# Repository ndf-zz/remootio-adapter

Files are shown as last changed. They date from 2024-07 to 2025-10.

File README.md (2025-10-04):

# Remootio Adapter "PLC" - Hay Hoist

Adapt a Remootio door opener remote to
a golf buggy motor controller using an
AVR m328pb for remote control of a hay hoist.

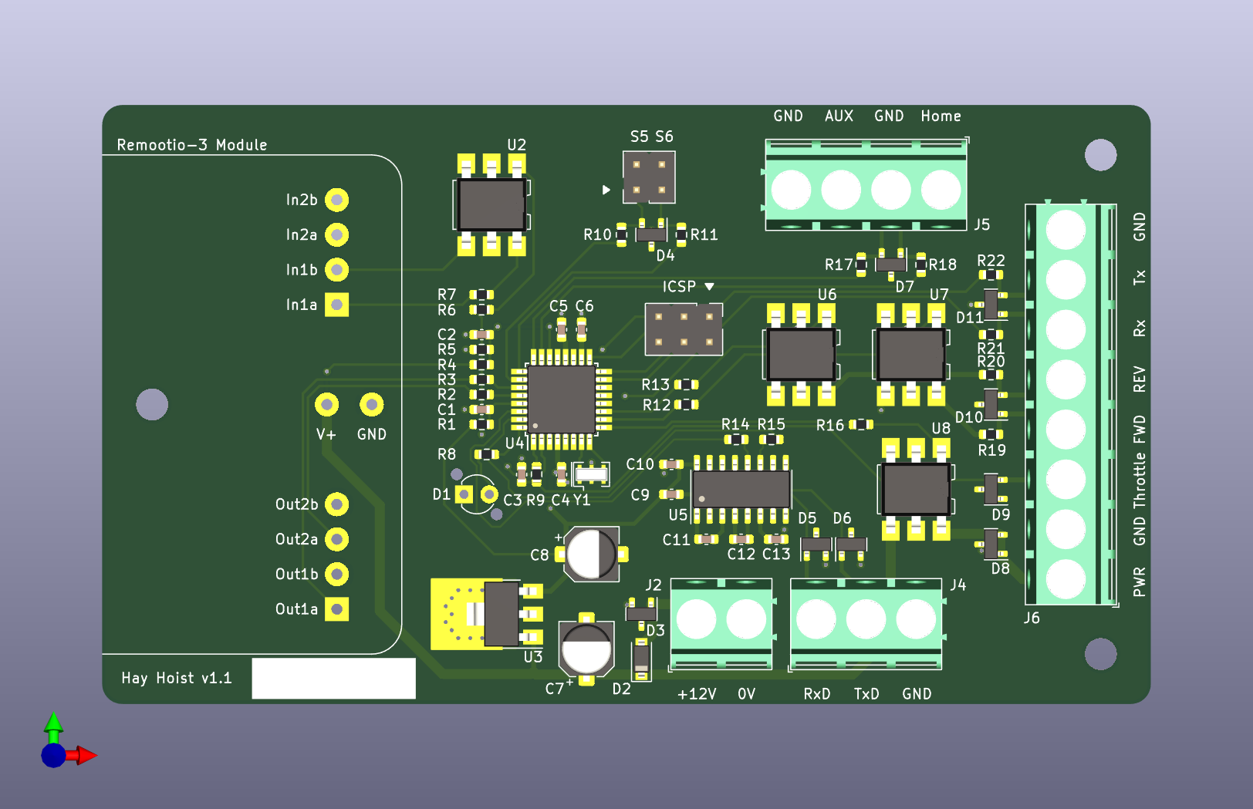
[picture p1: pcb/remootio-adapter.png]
PCB


## Operation

### Manual Operation

On reception of "down" command, hoist is lowered to P1 height.
If no further commands are received, it will retract to the home
position after the configured feed time minutes have elapsed.

A further "down" command will lower the hoist to the P2 height.

Return to home position on reception of an "up" signal, or
after a programmable duration without input.

State Machine State Diagram

### Automated Feeding

If a number of feeds per week is specified, the hoist will lower
from the home position to P1 after a randomly chosen interval,
roughly "feeds/week" times a week and provided there is enough
charge in the battery to retract.

The hoist will remain at P1 until feed time minutes have elapsed, 
then retract to the home position. Manual operation "down" or
"up" will cancel a pending automatic operation.

To disable automated feeding, manually lower the hoist slightly
from the home position. To re-enable, return hoist to home
("open") position.

### Special Cases

If an error condition is flagged, the hoist will only allow
movement up and down small amounts determined by the "Man time"
setting. To correct an error state, clear the sensor
switch and then manually operate the hoist down slightly and
then up to the home position.

Errors and exceptions may be triggered by the following conditions:

   - Low Battery: Automated feeding is suppressed when battery
     voltage falls below 13V. In this state, manual operation
     is still enabled. If the battery falls below 11.8V,
     a warning LED is illuminated and remootio operation is disabled.
   - Spurious Sensor: In the case of a spurious triggering of
     the home sensor, an error condition is flagged and the
     motor is stopped.
   - Not at Home: If the home sensor is prematurely
     triggered, the hoist will attempt to continue retraction
     after Home-Retry seconds.
   - Sensor Failure: If the home sensor fails "open", or if the
     state logic is out of sync, the hoist will not react to
     up (raise) commands. If the sensor fails "closed", and max
     H time has elapsed, the hoist will flag an error condition.
   - Safetime: If the hoist is left at position P2, between P1 and P2,
     or in the STOP state, it will attempt to retract automatically
     to the home position after about 60 minutes.
   - Disable Automation: Automated random feeding may be temporarily
     disabled by manually lowering the hoist slightly from the home
     position to state "STOP H-P1". To re-enable random feeding, return
     hoist to home position.

### Serial Console

**Note**: Serial console is not available on units supplied with
BLE adapter.

Connect RS-232 serial adapter to J4 (console)
and open a terminal at 19200 baud, 8n1.

Enter 'p' followed by pin number and enter to enable
console.

Triggers, state changes and errors will
be displayed.

Enter '?' to display available commands:

	Commands:
	        1       H-P1 (0.01s)
	        2       P1-P2 (0.01s)
	        m       Man (0.01s)
	        h       H (0.01s)
	        r       H-Retry (0.01s)
	        f       Feed (minutes)
	        n       Feeds/week (0=off)
	        v       Show values
	        s       Status
	        d       Lower
	        u       Raise

Configuration parameters are adjusted
by entering the command key followed by
an updated value and then enter.
Time values 1,2,m,h and r are set in units of 0.01s.
Feeding time f is in minutes.

## Connectors

Adapter | Connector | Description
--- | --- | ---
J1:1 |  | "S5" Auxiliary I/O (unused)
J1:2 |  | "GND"
J1:3 |  | "S6" Auxiliary I/O (unused)
J1:4 |  | "GND"
N/C | C3:B | Motor + (blue/black)
N/C | C3:C | Motor - (yellow/red)
J2:1 | C4:D | "+12V" Battery + (red)
J2:2 | C4:A | "0V" Battery - (black)
J3:1 |  | ICSP MISO
J3:2 |  | ICSP VCC
J3:3 |  | ICSP SCK
J3:4 |  | ICSP MOSI
J3:5 |  | ICSP RST
J3:6 |  | ICSP GND
J4:1 | C1:2 | "RxD" Console DCE Received Data (brown)
J4:2 | C1:3 | "TxD" Console DCE Transmitted Data (yellow)
J4:3 | C1:5 | "GND" Console DCE Common Ground (white)
J5:1 | C2:C | "Home" Home Limit Input (NC output green)
N/C | C2:B | Short to C2:D (green)
J5:2 | C2:A | "GND" Home Limit Ground (blue)
N/C | C2:D | Short to C2:B
J5:3 |  | "AUX" Encoder/Counter Input (unused)
J5:4 |  | "GND" Encoder/Counter Ground
J6:1 | M1:7 | "PWR" Controller power (pink)
J6:2 | M:6,20 | "GND" Controller ground (black)
J6:3 | M:3 | "Throttle" Controller speed (green)
J6:4 | M:12 | "FWD" Controller forward (white)
J6:5 | M:14 | "REV" Controller reverse (orange)
J6:6 | M:Rx | "Rx" Controller serial receive (blue)
J6:7 | M:Tx | "Tx" Controller serial transmit (green)
J6:8 | M:Gnd | "GND" Controller ground (black)

## Firmware

### Source Layout

	Main event loop:		src/main.c: 	main()
	State machine logic:	src/main.c:		update_state()
	Reset/initialisation:	src/system.c:	system_init()
	Serial console logic:	src/console.c:	read_input()
	SPM controller setting:	src/spmcheck.c	spm_check()

### Version Summaries

   - 25003: BLE adapter updates, October 2025
      - include system clock with state summary
      - adjust low battery override states
      - extend console idle timeout to 5 minutes
      - extend safe time to 60 minutes
   - 25002: Version 2.1, ignore home trigger when at P1
   - 25001: Version 2
      - include Home Retry option & logic
      - add trivial plaintext 'passkey' to protect serial console
   - 24012: Version 1, cosmetic updates for GUI tool, October 2024
   - 24011: Version 0, initial release September 2024

## Build

Connect AVR ISP to programming header, program fuses, initialise
the random seed book, then build and upload firmware to MCU:

	$ make fuse
	$ make randbook
	$ make upload

Note: randbook will overwrite any stored configuration, so it should
only be run once when initialising a new unit. Uploading a new
firmware will not overwrite stored configuration.

On boot, the SPM controller will be updated if required. Updates are
reported to the console output:

	Info: Boot v24011
	SPM: Config updated
	Info: Boot v24011
	SPM: 23014810
	Trigger: reset
	State: [STOP] Batt: 0.0V
	Trigger: home
	[...]

## Build Requirements

   - GNU Make
   - gcc-avr
   - binutils-avr
   - avr-libc
   - avrdude
   - python3 (if controller config is edited)

On a Debian system, use make to install required packages:

	$ make requires

## Production Unit Info

   - [assembly/](assembly/ "Assembly instruction")
   - [assembly/burn-in.sh](assembly/burn-in.sh "Burn-in"):
     Prepare unit for first-time use.
   - [assembly/update25001.sh](assembly/update25001.sh "Update to v25001+"):
     Update unit with firmware < v25001, retaining configuration.

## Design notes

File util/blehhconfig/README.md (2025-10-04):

# Hay Hoist Bluetooth Configuration Tool

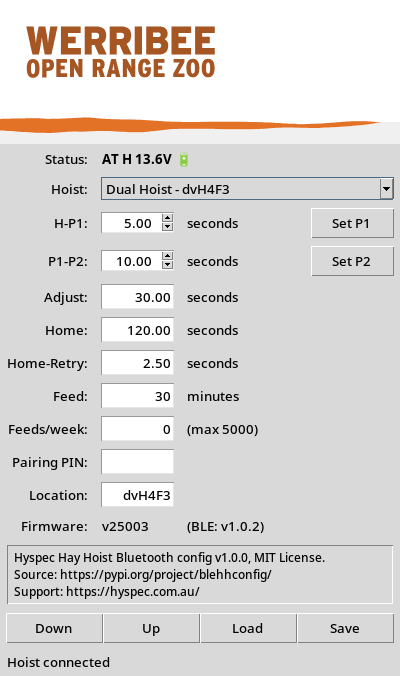
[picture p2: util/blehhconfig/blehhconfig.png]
blehhconfig screenshot


Configure Hay Hoist connected via a
[bleuart](https://github.com/ndf-zz/bleuart/)
Bluetooth to RS232 adapter.

## Usage

	blehhconfig [-v]

Launch blehhconfig utility, then select hoist from
devices list.

Current status is displayed on the top line. Use
"Down" and "Up" buttons to trigger the hoist. "Load"
and "Save" buttons read or write configuration
from/to a JSON text file.

Set P1 and Set P2 buttons measure time and update
a connected hoist accordingly.

## Installation

Install into a venv with pip:

	$ python -m venv hh
	$ ./hh/bin/pip install blehhconfig
	$ ./hh/bin/blehhconfig

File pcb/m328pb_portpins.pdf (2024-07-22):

Hay Hoist - ATmega328PB Port/Pin Allocation

Date: 2024-07-22

# Channel

Port | 0 | 1 | 2 | 3 | 4 | 5 | 6 | 7
B | | | | X | X | S | S | S | Unused/Not available
| | | | MTX | MRX | SCK | XTAL1 | XTAL2
C | I | I | I | I | I | I | S | | USART
| S1 | S2 | S6 | S5 | S3 | S4 | RESET
D | X | X | O | X | O | O | O | O | Out
| CRX | CTX | LED | V1(PWM) | R4 | R3 | R1 | R2
E | | | | A | | | | | In
| | | | A1
| Pin Modes | | Signals
I: Digital Input | V1 | Throttle (0-5V) | S1 - S6 | Switch Inputs 1-6
O: Digital Output | A1 | Battery Sense | R1 - R4 | Relay Outputs 1-4
A: Analog | MTX/RX | Motor Serial Port | LED | Indicator LED
X: Alternate Function | CTX/CRX | Console Serial Port

S: Additional Function

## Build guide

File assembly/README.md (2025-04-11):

# Assembly Instruction

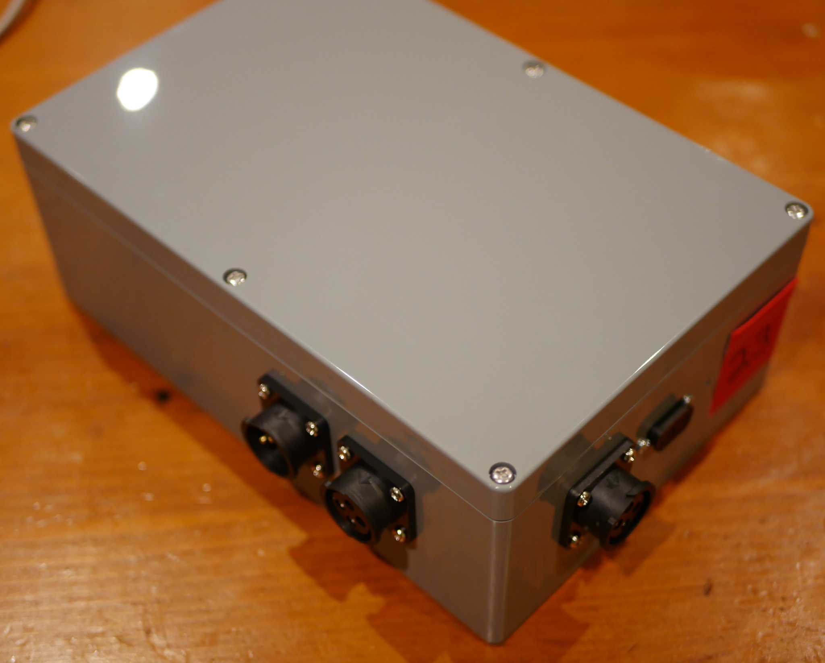
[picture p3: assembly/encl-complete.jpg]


## Components

   - Remootio Module
   - Main PCB
   - Motor Controller
   - Connectors
   - Mounting Plate
   - Enclosure
   - AC Power Supply

## Remootio Module

Power on Remootio using supplied DC adapter, pair with
application and then setup as follows:

   - Select output configuration 4: "Output 1 to open, Output 2 to close"
   - Configure both "open" and "close" impulse length to 50ms.
   - Disable background display option
   - Under power settings enable "Low Power Mode" and "Dark Mode"
   - Enable sensor add-on: Input 1

Test operation with application, then prepare PCB for use with
adapter:

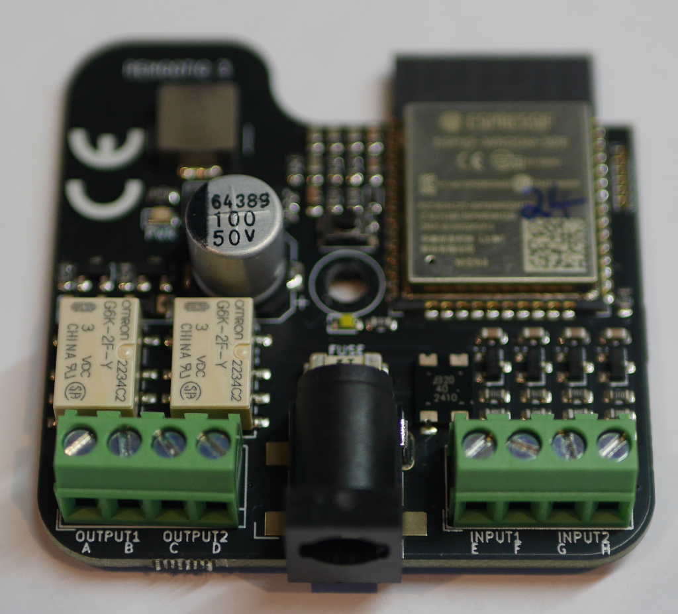
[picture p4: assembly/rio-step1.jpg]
Remove Enclosure


Remove Remootio from plastic enclosure.

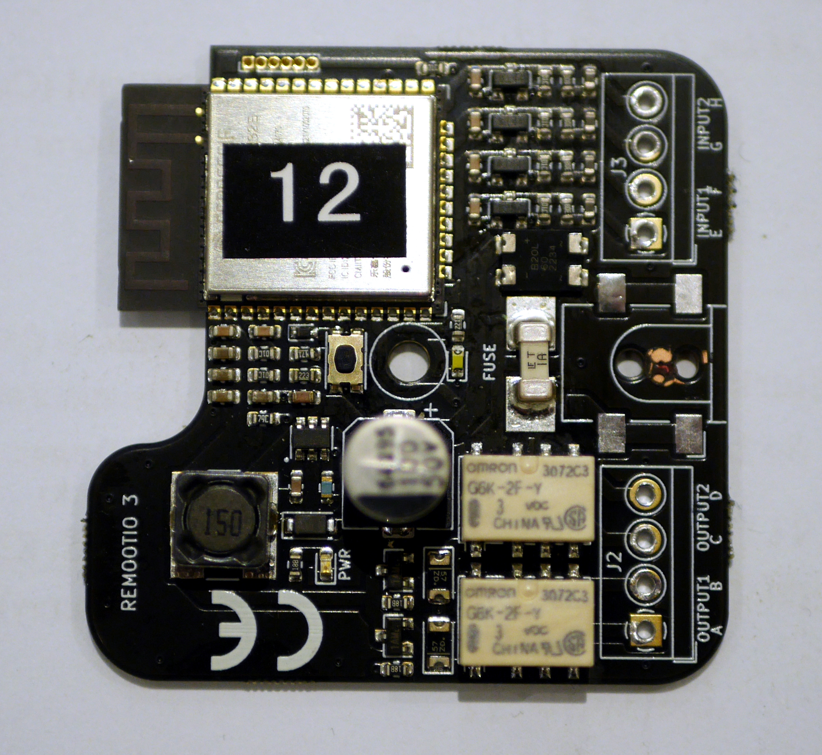
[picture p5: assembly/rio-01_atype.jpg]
SMT Variant SMT DC Variant


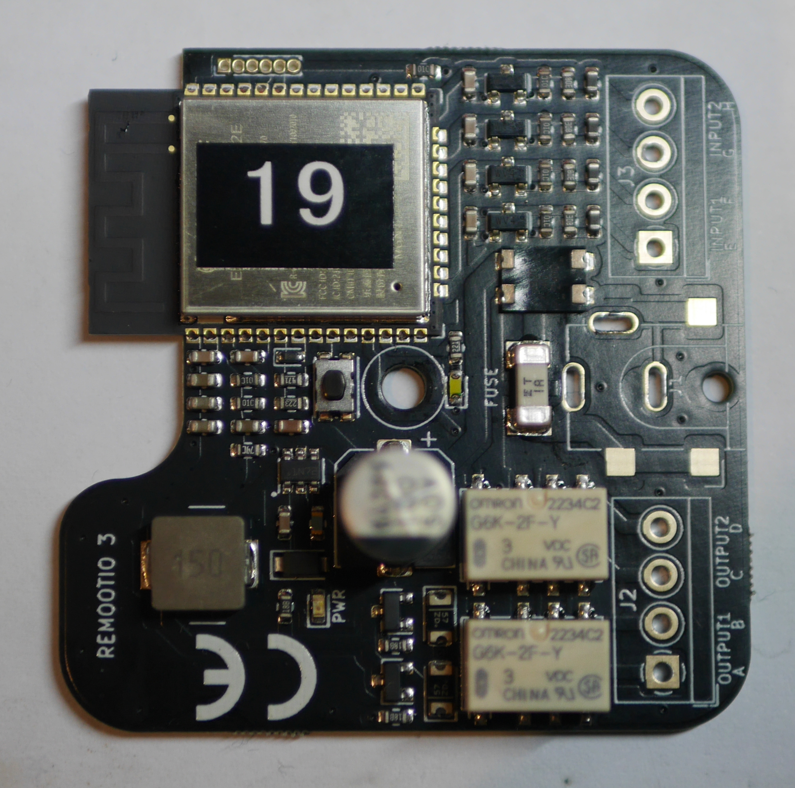
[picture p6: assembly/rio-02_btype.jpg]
THT Variant THT DC Variant


De-solder DC socket and screw terminal blocks.

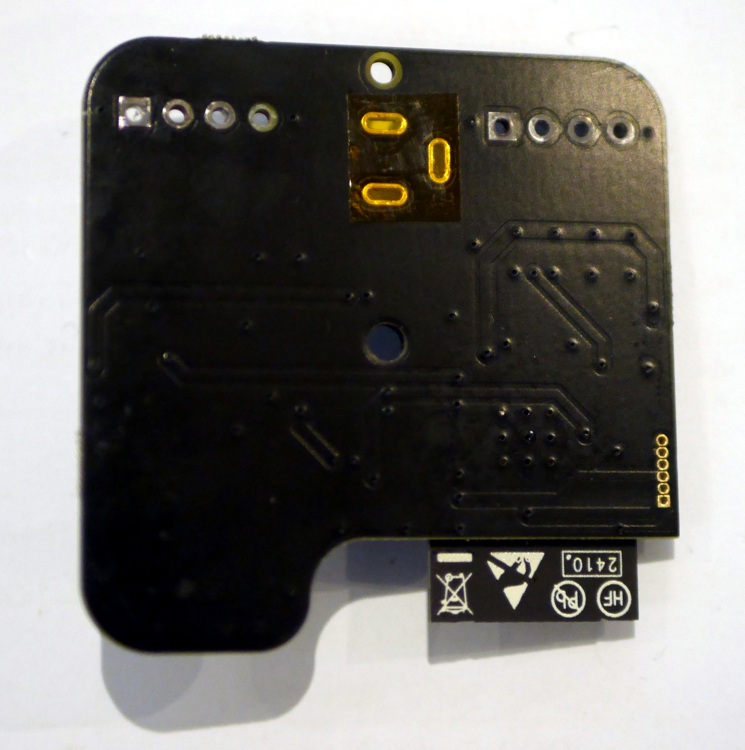
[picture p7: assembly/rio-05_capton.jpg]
Capton THT THT Capton Tape


If DC connector is through-hole type, place a strip of capton tape
over bottom-side pads.
For both variants, place small length of
capton tape over DC jack alignment hole(s) on top side.

Label module with serial number for future reference.

## Main PCB

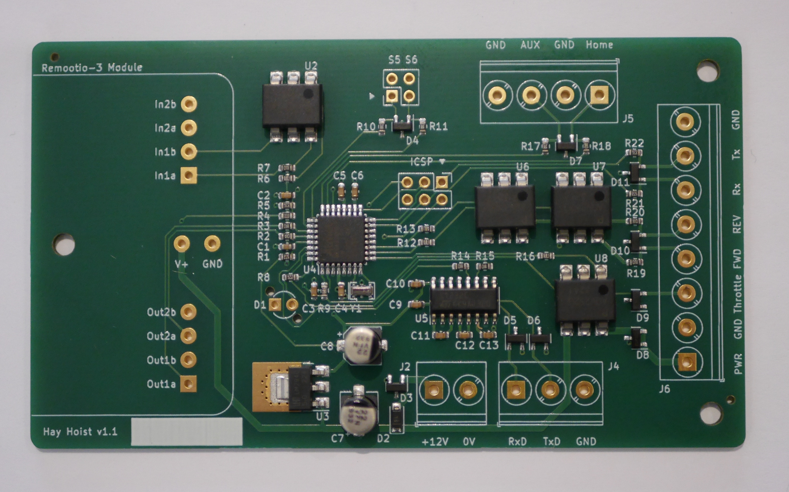
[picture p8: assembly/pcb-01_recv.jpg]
Inspect Inspect PCB


Inspect PCB for clean solder joints, parts properly located
and finish.

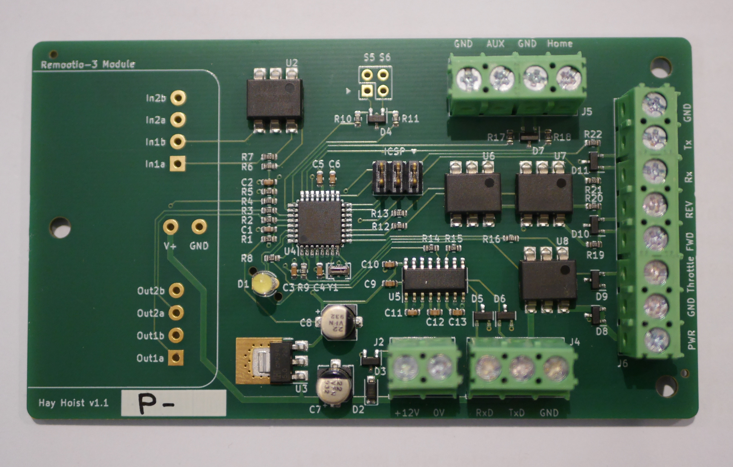
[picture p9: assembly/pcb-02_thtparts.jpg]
THT Parts Solder THT Parts


Solder THT parts to PCB:

   - ICSP header J3
   - Screw terminals J2, J4, J5, J6
   - LED D1 with ~4mm standoff from board

Perform the following tests:

   - connect console C1 and 12V
   - connect ICSP
   - power on
   - run burn-in.sh
   - observe boot sequence
   - verify home trigger
   - stimulate home trigger, observe console
   - short home trigger
   - command up, check for spurious warning
   - set meter to Volts, command down
      - check PWR at ~12V
      - check Throttle at ~5V
   - set meter to continuity
      - check In1a/b for short AT-P1
      - Check FWD & REV open to GND
      - command up/down & check FWD/REV short to GND
   - observe console
      - trigger Out1a/b and Out2a/b for up/down trigger
   - pass => write "P-" on serial no panel

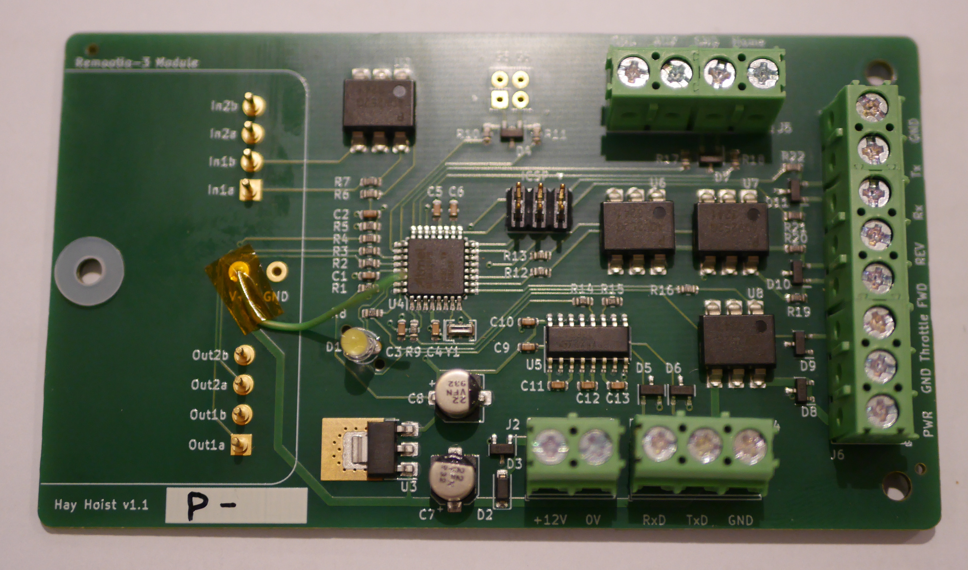
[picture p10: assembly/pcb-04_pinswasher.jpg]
RIO Mounting Remootio Pins


Insert Remootio module mounting pins (do not solder). If Remootio
is THT type, insert a short bodge wire as pictured and
cover with capton tape. Position 2x spacing washers over mounting
hole, then lower module into place and fix with screw.

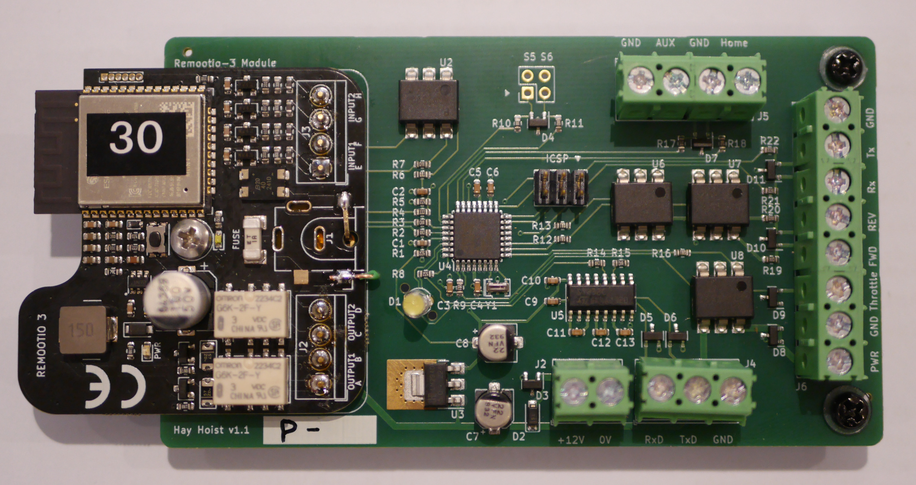
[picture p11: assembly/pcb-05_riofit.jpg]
THT RIO Solder THT Type Soldered


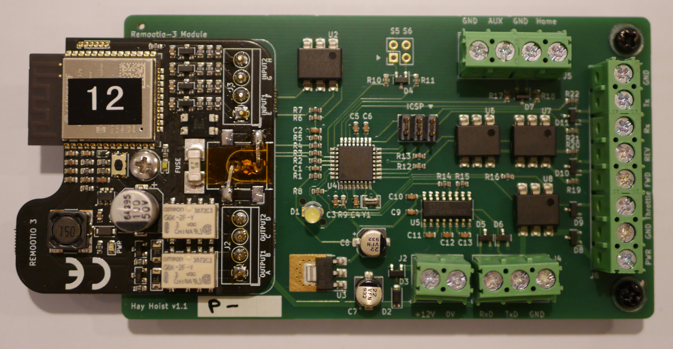
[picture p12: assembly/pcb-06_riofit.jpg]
SMT RIO Solder SMT Type Soldered


Solder mounting pins and power links from top side, then flip
board and solder bottom side.

Power on unit and check operation of Remootio on adapter.

## Motor Controller Preparation

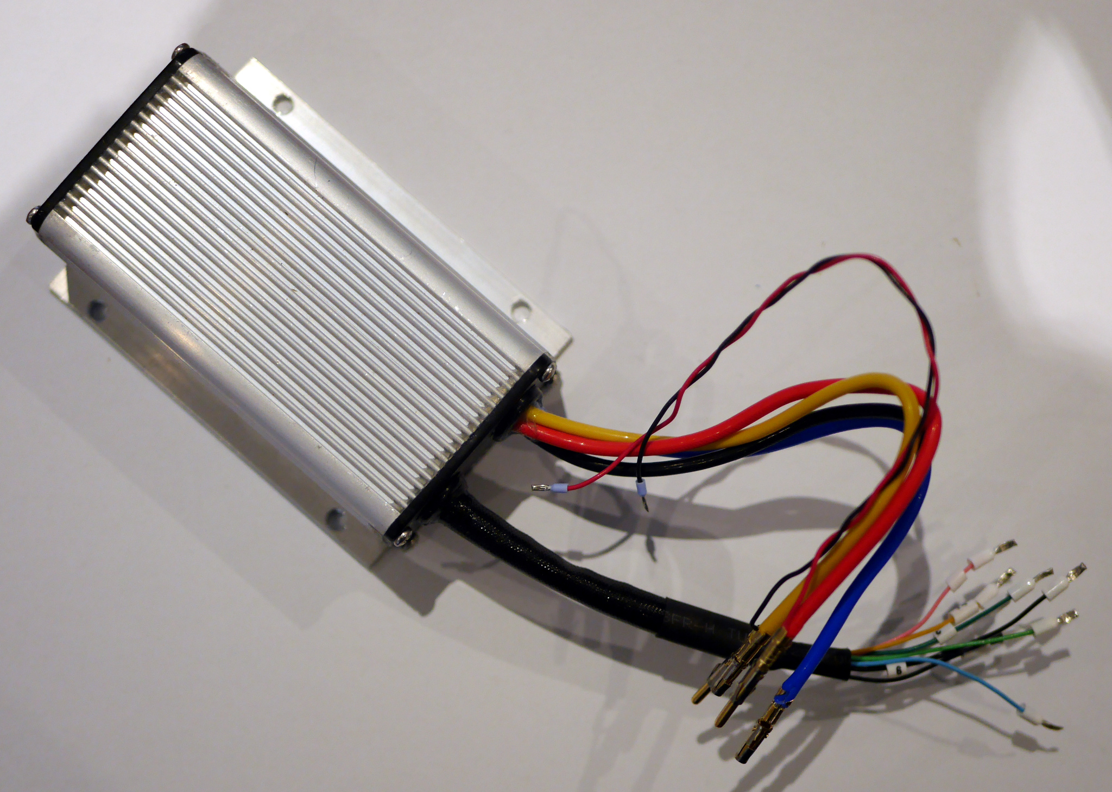
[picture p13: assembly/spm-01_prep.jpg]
Motor Controller


Shorten cable sleeve 15-20mm. At the serial connector,
cut the red (V+) wire. At the other connectors,
cut the following unused wires:

   - 1 Raddle[sic] (BRK2)
   - 2 Dark Gray (Brake AN)
   - 4 Purple (5V)
   - 8 Blue (Meter)
   - 9 Light Blue (Relay)
   - 10 Yellow (Alarm)
   - 11 Red (12V)
   - 13 Brown (BRK_SW)
   - 15 Gray (Micro SW)
   - 22 Blue/Green (undocumented)

Thread unused wires under heat-shrink, check required
wires are still attached, then cut short.
Terminate required wires with crimp ferrules:

   - 7 Pink J6:1 (PWR)
   - 6 & 20 Black J6:2 (GND, terminate together)
   - 3 Dark Green J6:3 (Throttle, may be light green)
   - 12 White J6:4 (FWD)
   - 14 Orange J6:5 (REV_SW, may be yellow)
   - Serial Blue J6:6 (Rx)
   - Serial Green J6:7 (Tx)
   - Serial Black J6:8 (GND)

Terminate blue and yellow motor leads with female
crimp terminals (SS12A1F).

Twist ~200mm length of red and black hookup wire on to
corresponding battery leads, then terminate with male
crimp terminals (SP12A1F).

Terminate loose ends of red/black hookup wires with crimp ferrule.

Motor controller is configured by firmware at boot time
as necessary according to
[spm_config.bin](../reference/spm_config.bin)
and [spm_config.txt](../reference/spm_config.txt).

Use [spmtool](https://github.com/ndf-zz/spmtool) to create
a new configuration if required. Settings match the following in
Kelly Controller software:

### Step 1: General Setting

   - Forward Switch: Enable
   - Foot Switch: Disable
   - Throttle Sensor Type: 0-5V
   - Throttle Effective Starting: 4%
   - Throttle Effective Ending: 96%
   - Max Motor Current: 85%
   - Max Battery Current: 40%

### Step 2: General Setting

   - Start-up Delay: 0 sec
   - Control Mode: Balanced
   - Under voltage: 10V
   - Over Voltage: 20V
   - Throttle Up/Down Rate: 1 (Fast)
   - Power On High Pedal Disable: Disable
   - Releasing Brake High Pedal Disable: Disable

### Step 3: General Setting

   - Motor Top Speed: 100%
   - Boost Function: Disable
   - Economy Function: Disable
   - Half Current in Reverse: Disable
   - ABS: Disable
   - 12V Output: Disable
   - Motor Top Speed in Reverse: 100%
   - Joysticker[sic] Throttle: Disable

### Step 4: Regeneration Setting

   - Regeneration: Disable
   - Brake Switch: Disable
   - Releasing Throttle Starts Regen: Disable
   - Regen Current By Brake Switch On: 5% [unused]
   - Max Regen Current: 20% [unused]
   - Brake Sensor Type: No
   - Brake Sensor Starting Point: 0% [unused]
   - Brake Sensor Ending Point: 100% [unused]

### Step 5: Sensor, CAN, Smooth Setting

   - Motor Temperature Sensor: Disable
   - Controller Stop Output Temperature: 125C
   - Controller Resume Output 90C
   - CAN [empty]
   - Smooth: Disable

## Console Port C1

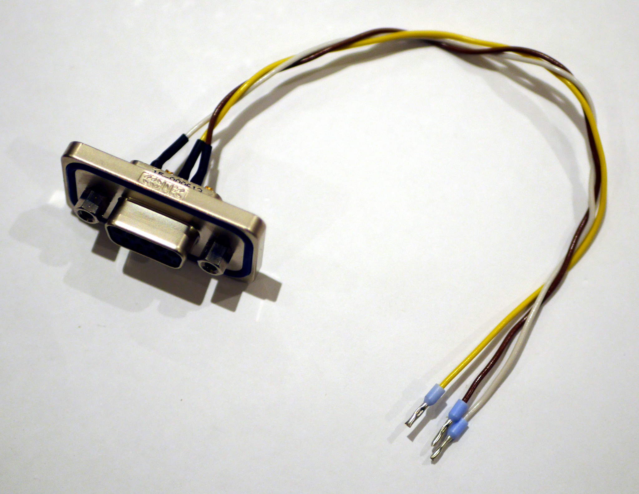
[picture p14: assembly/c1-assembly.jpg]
Console Port Console Port C1


Solder ~170mm wires to console dsub-9 (15-000613)
pins as follows:

   - Brown: C1:2 / J4:1 "RxD"
   - Yellow: C1:3 / J4:2 "TxD"
   - White: C1:5 / J4:3 "GND"

Terminate J4 ends with crimp ferrule.

## Sensor Port C2

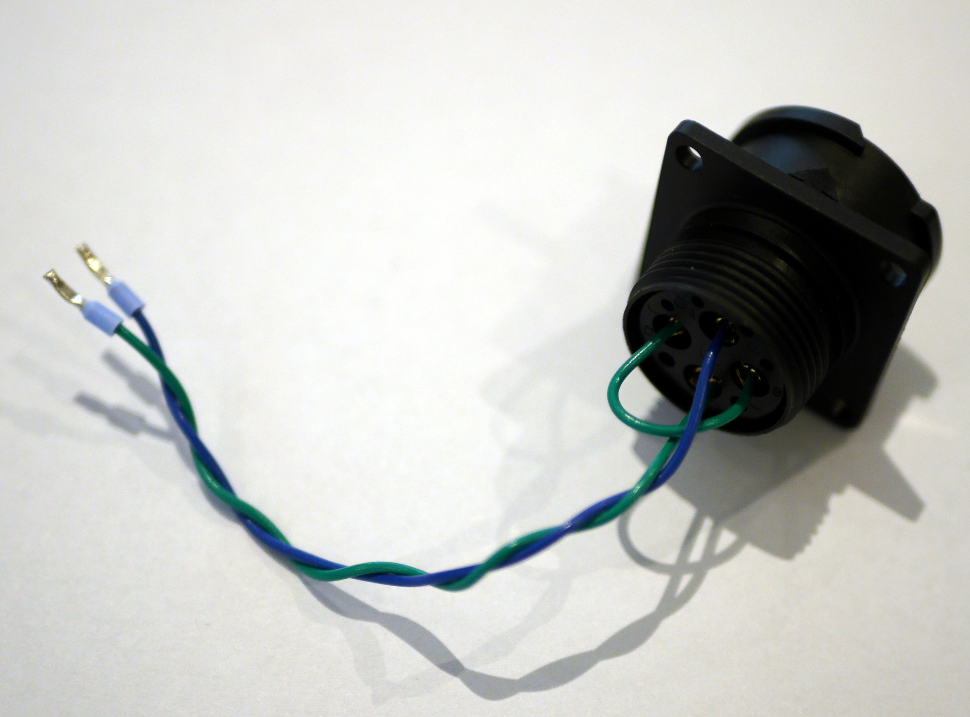
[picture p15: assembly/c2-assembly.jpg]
Sensor Port Sensor Port C2


Terminate ~90mm wires to female connector (SS12A1F):

   - Blue: C2:A / J5:2
   - Green: C2:C / J5:1

Short C2:B to C2:D with short link wire (green) and install
in female panel socket (FLS014N4S03-PM). Terminate
J5 ends with crimp ferrule.

## Enclosure

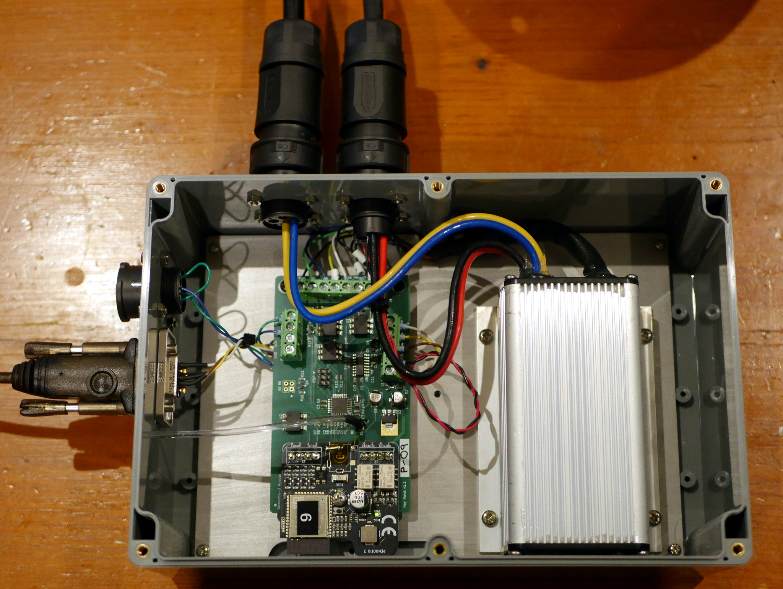
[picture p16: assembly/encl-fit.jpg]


   - Drill 2.9mm LED hole and D-SUB corners
   - Drill 3.2mm mounting holes and connector centres
   - Drill 5.5mm D-SUB corners
   - Enlarge connector holes to 21.0mm
   - Route D-SUB edges
   - Remove Burrs
   - Mount connectors to outside of case, add screws and fix
     with a small amount of thread lock on the nuts
   - Assemble PCB and motor controller on mounting plate
   - Connect wiring sub-assemblies to PCB
   - Lower complete mounting plate into box, fix with 4x M3
     screws with a small amount of thread locker
   - Insert sensor wires into connector
   - Mount D-SUB connector and tie leads to sensor wires
   - Thread LED pipe from outside box
   - Place 25mm length of heat-shrink over LED, insert LED pipe
     and shrink
   - Insert power cables and motor cables
   - Check operation in test harness
   - Fit lid and tighten

## AC Power Supply (indoor units)

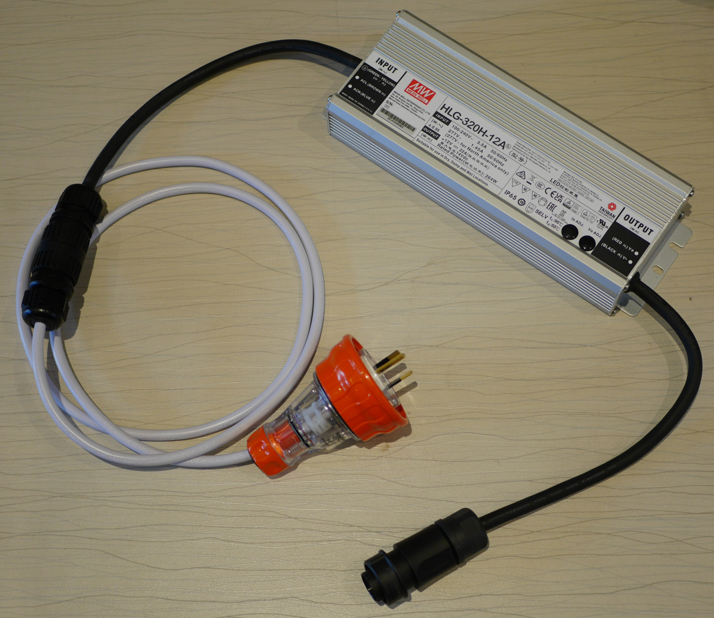
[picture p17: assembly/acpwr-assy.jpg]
AC Assembly AC Adapter Assembly


Prepare 12V connector (FLS6BS14N4S03):

   - insert rubber gland into backshell
   - slip nut and backshell over wire
   - terminate 12V lead with female terminals (SS12A1F)
   - insert 0V (black) terminal into position A
   - insert +12V (red) terminal into position D
   - tighten backshell and lock nut

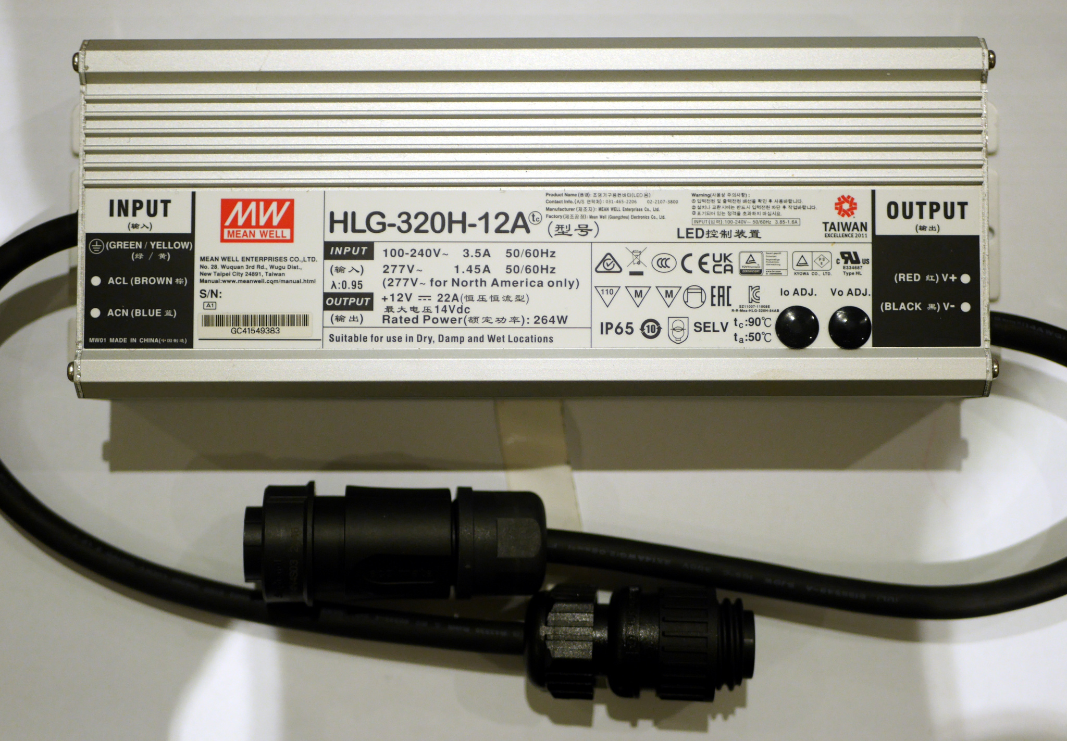
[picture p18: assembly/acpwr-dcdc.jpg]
Adapter AC Adapter


Prepare mains input plug (CA3LS):

   - crimp red ferrule on A, N and E wires
   - insert rubber gland into backshell
   - slip nut and backshell over wire
   - screw terminals into plug:
      - E position "PE"
      - A position 1
      - N position 2
   - tighten backshell and lock nut

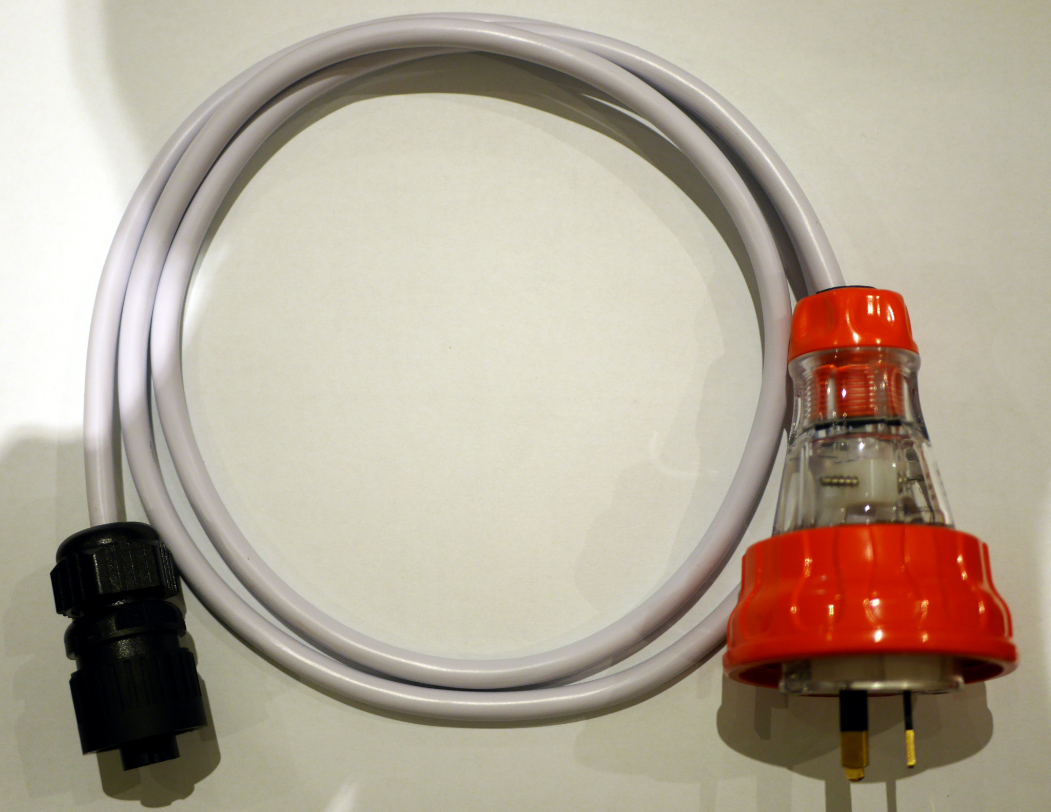
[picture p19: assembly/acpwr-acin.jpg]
AC Extension


Prepare mains extension lead:

   - cut mains lead to required length ~1500mm
   - strip ~28mm leads on both ends
   - terminate all ends with red crimp ferrules
   - mount captive IEC plug as per manufacturer instruction
   - insert rubber gland in plug backshell (CA3LD)
   - slip nut and backshell over wire
   - screw terminals into plug:
      - E position "PE"
      - A position 1
      - N position 2
   - tighten backshell and lock nut

Connect to power and box, then adjust Vo to 13.5V
Confirm Battery reading in config tool between 13.3 and 13.6V

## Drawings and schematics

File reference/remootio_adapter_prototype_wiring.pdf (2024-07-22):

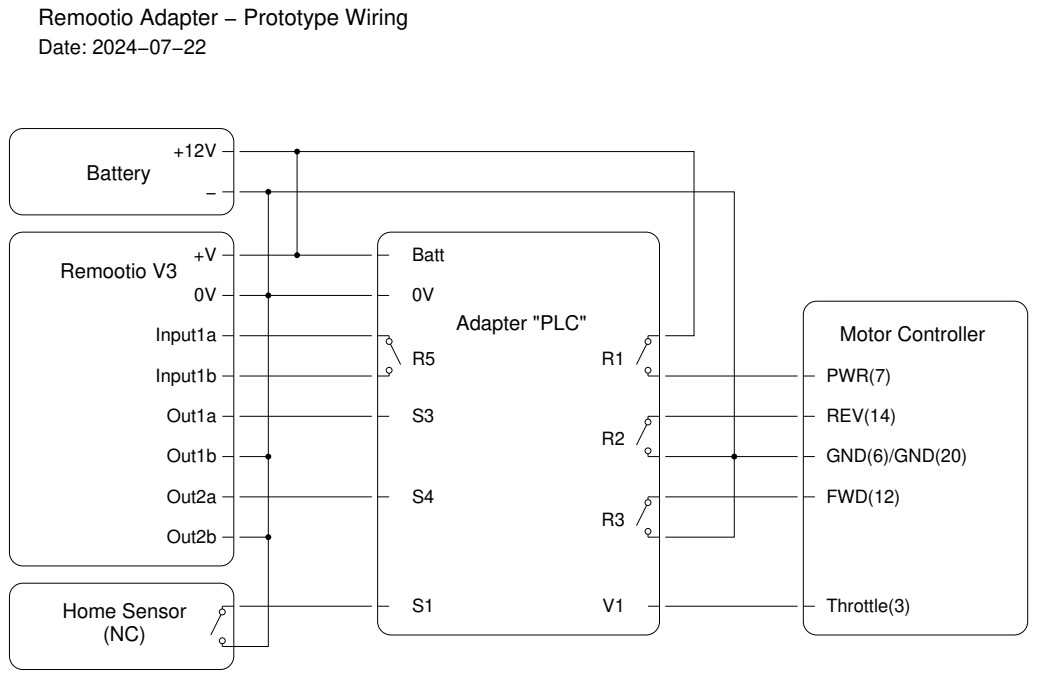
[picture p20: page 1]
Battery; Out1a; Input1a; Input1b; Out1b; Out2a; Out2b; Remootio V3; Home Sensor (NC); Adapter "PLC"; Throttle(3); REV(14); FWD(12); PWR(7); GND(6)/GND(20); Motor Controller; Batt

Remootio Adapter − Prototype Wiring
Date: 2024−07−22

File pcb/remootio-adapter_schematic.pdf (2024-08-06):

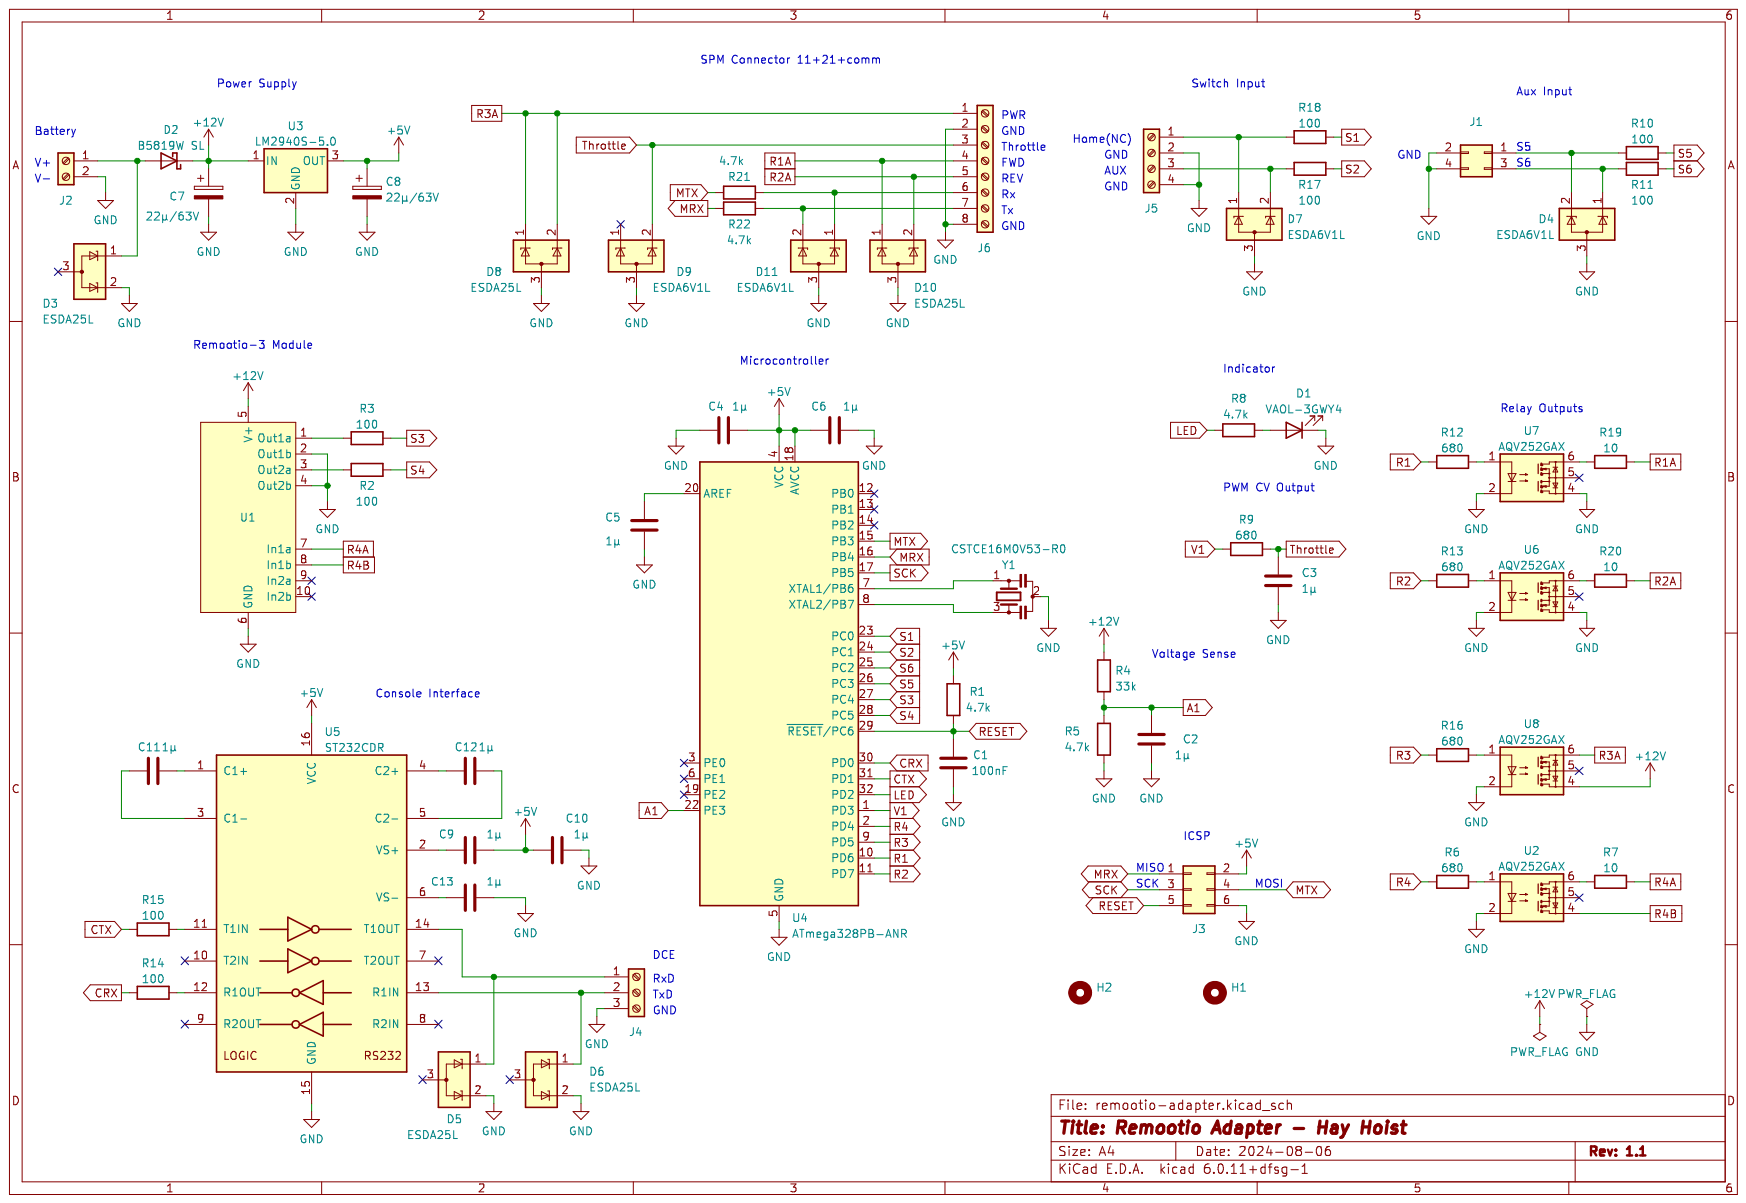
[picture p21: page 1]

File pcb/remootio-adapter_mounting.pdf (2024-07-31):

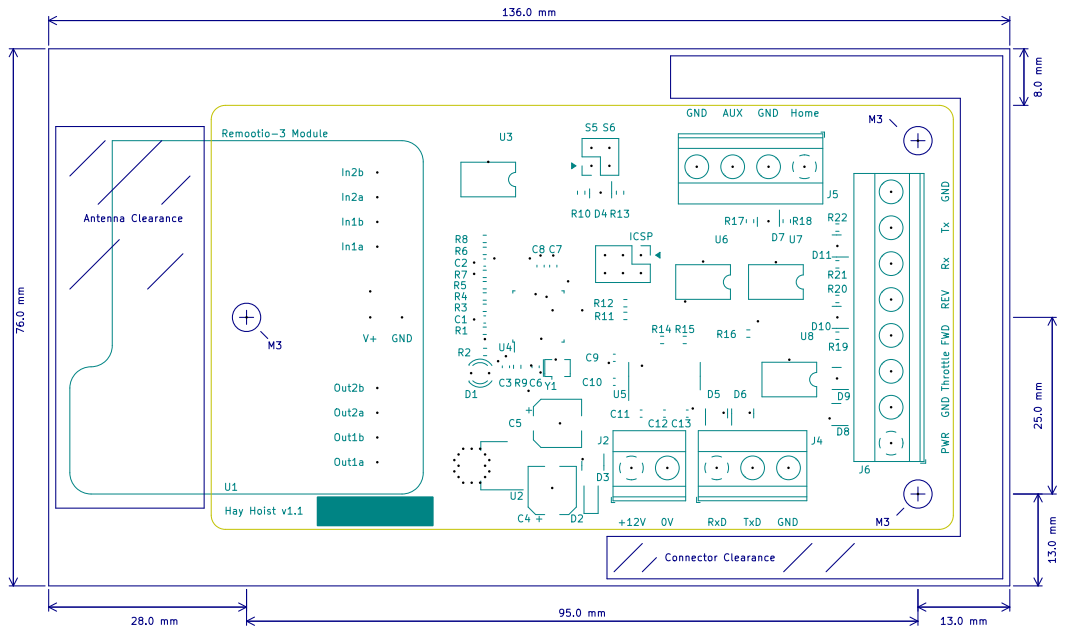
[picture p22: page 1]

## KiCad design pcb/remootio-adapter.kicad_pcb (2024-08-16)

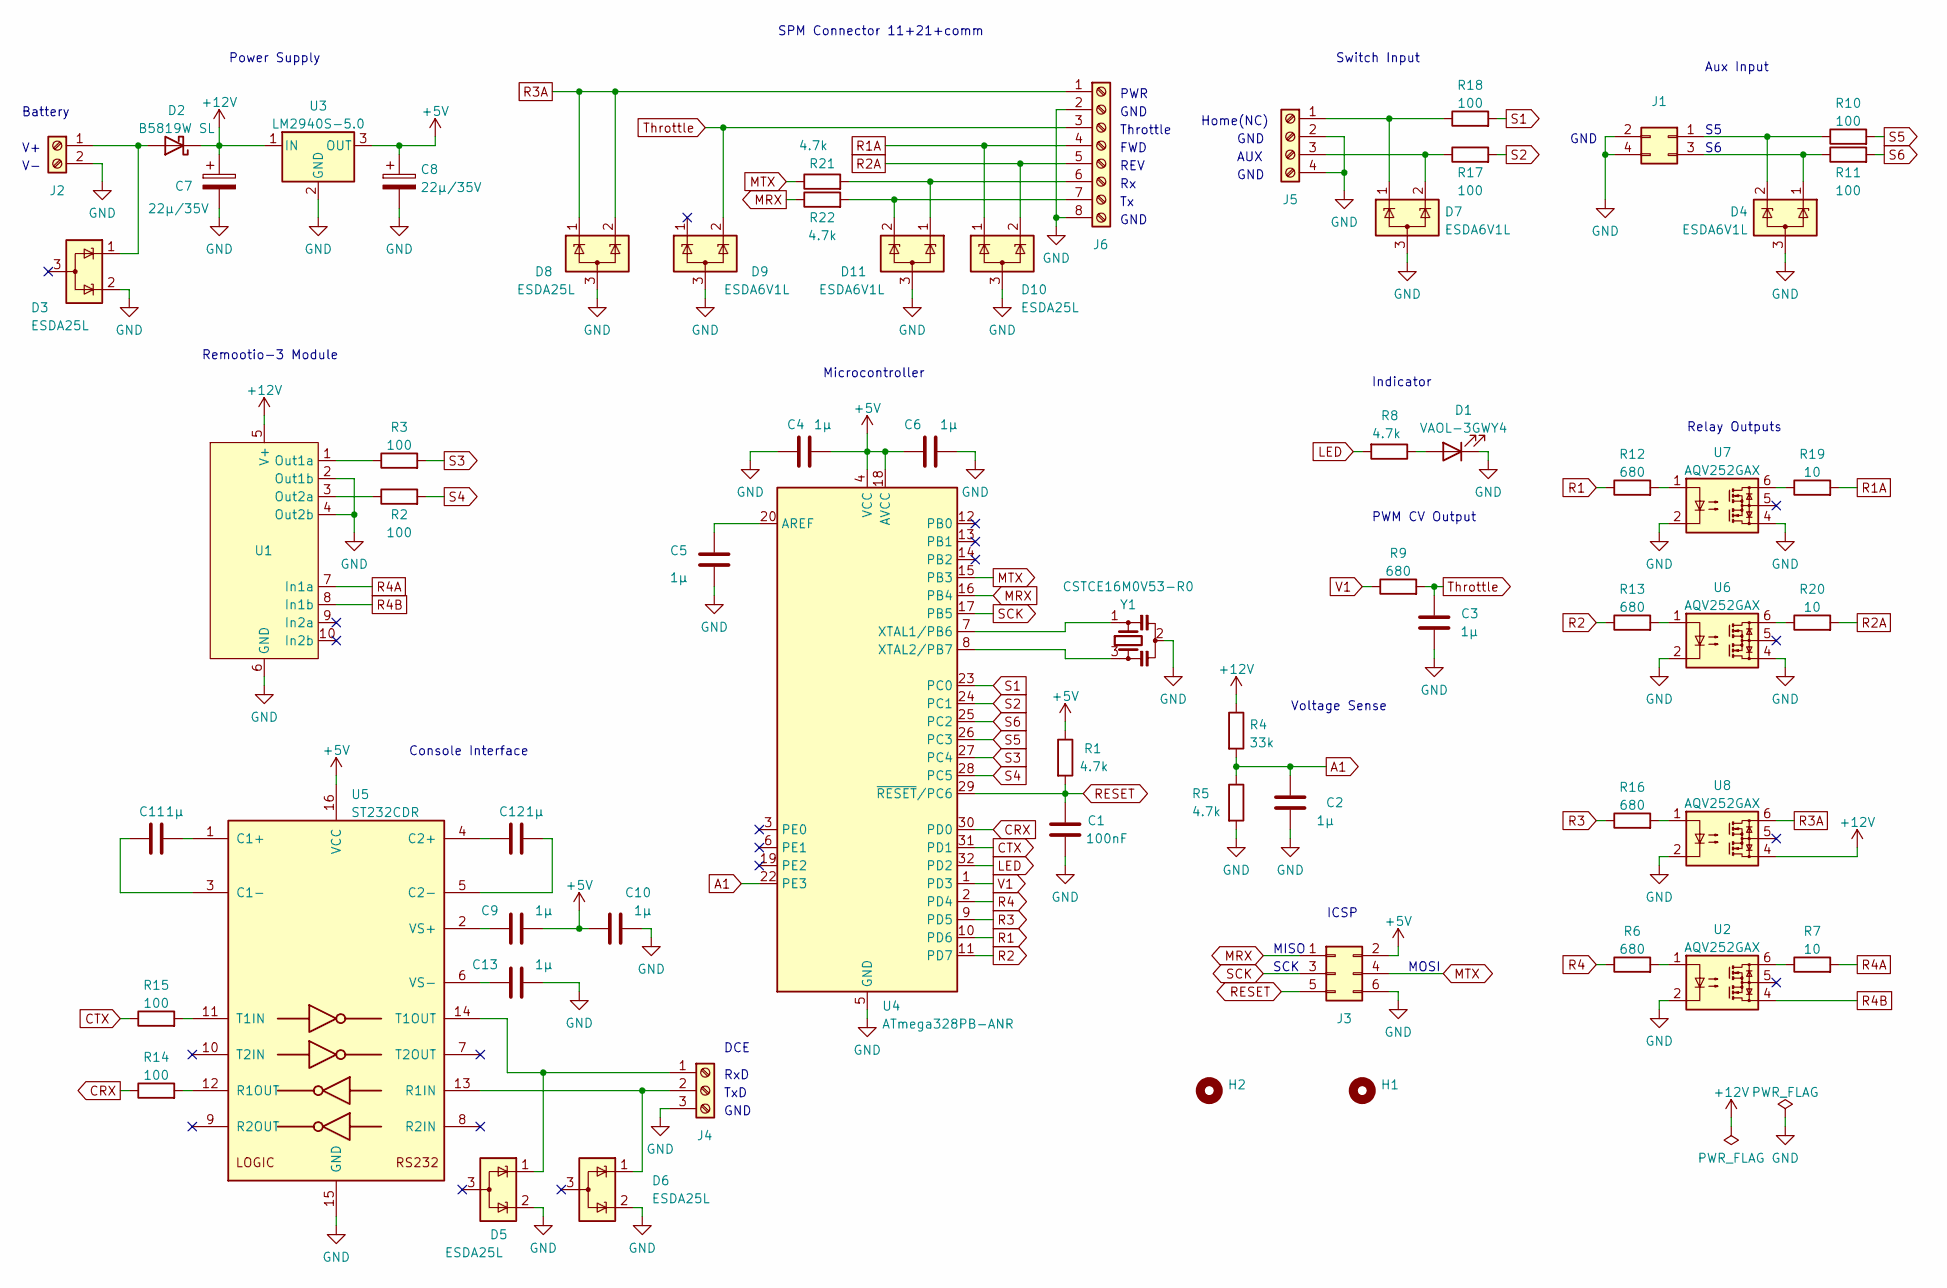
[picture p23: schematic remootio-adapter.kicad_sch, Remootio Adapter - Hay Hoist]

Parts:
C1: 100nF; C_0603_1608Metric; PARTNO CC0603KRX7R9BB104; LCSC C14663
C2, C3, C4, C5, C6, C9, C10, C11, C12, C13: 1µ; C_0603_1608Metric; PARTNO GRM188R71E105KA12D; LCSC C86020
C7, C8: 22µ/35V; CP_Elec_5x5.8; PARTNO EEEFN1V220R; LCSC C494835
D1: VAOL-3GWY4; bivar-led
D2: B5819W SL; D_SOD-123; LCSC C8598
D3, D5, D6, D8, D10: ESDA25L; SOT-23; LCSC C95343
D4, D7, D9, D11: ESDA6V1L; SOT-23; LCSC C24378
H1, H2: MountingHole; MountingHole_3.2mm_M3
J1: AUX; PinHeader_2x02_P2.54mm_Vertical; Partno DNP
J2: BATT; TerminalBlock_Phoenix_PT-1,5-2-5.0-H_1x02_P5.00mm_Horizontal; Partno 1935161
J3: ICSP; PinHeader_2x03_P2.54mm_Vertical; Partno 702871099
J4: Console; TerminalBlock_Phoenix_PT-1,5-3-5.0-H_1x03_P5.00mm_Horizontal; Partno 1935174
J5: SwitchIn; TerminalBlock_Phoenix_PT-1,5-4-5.0-H_1x04_P5.00mm_Horizontal; Partno 1935187
J6: SPM Connector; TerminalBlock_Phoenix_PT-1,5-8-5.0-H_1x08_P5.00mm_Horizontal
R1, R5, R8, R21, R22: 4.7k; R_0603_1608Metric; PARTNO 0603WAF4701T5E; LCSC C23162
R2, R3, R10, R11, R14, R15, R17, R18: 100; R_0603_1608Metric; PARTNO GRM188R71E105KA12D; LCSC C22775
R4: 33k; R_0603_1608Metric; PARTNO 0603WAF3302T5E; LCSC C4216
R6, R9, R12, R13, R16: 680; R_0603_1608Metric; PARTNO 0603WAF6800T5E; LCSC C23228
R7, R19, R20: 10; R_0603_1608Metric; PARTNO 0603WAF100JT5E; LCSC C22859
U1: remootio-3
U2, U6, U7, U8: AQV252GAX; SMDIP-6_W7.62mm; LCSC C425149
U3: LM2940S-5.0; SOT-223-3_TabPin2; LCSC C596334
U4: ATmega328PB-ANR; TQFP-32_7x7mm_P0.8mm; LCSC C2053137
U5: ST232CDR; SO-16_3.9x9.9mm_P1.27mm; LCSC C6869
Y1: CSTCE16M0V53-R0; Resonator_SMD_Murata_CSTxExxV-3Pin_3.0x1.1mm; LCSC C32180

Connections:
+5V: C4.1, C6.2, C8.1, C9.1, C10.2, J3.2, R1.1, U3.3 (OUT), U4.4 (VCC), U4.18 (AVCC), U5.16 (VCC)
+12V: C7.1, D2.1 (K), R4.1, U1.5 (V+), U3.1 (IN), U8.4
A1: C2.2, R4.2, R5.1, U4.22 (PE3)
CRX: R14.1, U4.30 (PD0)
CTX: R15.1, U4.31 (PD1)
GND: C1.1, C2.1, C3.1, C4.2, C5.2, C6.1, C7.2, C8.2, C10.1, C13.1, D1.1 (K), D3.2 (K), D4.3 (A), D5.2 (K), D6.2 (K), D7.3 (A), D8.3 (A), D9.3 (A), D10.3 (A), D11.3 (A), J1.2, J1.4, J2.2, J3.6, J4.3, J5.2, J5.4, J6.2, J6.8, R5.2, U1.2 (Out1b), U1.4 (Out2b), U1.6 (GND), U2.2, U3.2 (GND), U4.5 (GND), U4.21 (GND), U5.15 (GND), U6.2, U6.4, U7.2, U7.4, U8.2, Y1.2
LED: R8.2, U4.32 (PD2)
MRX: J3.1, R22.1, U4.16 (PB4)
MTX: J3.4, R21.1, U4.15 (PB3)
unnamed: C5.1, U4.20 (AREF)
unnamed: C9.2, U5.2 (VS+)
unnamed: C11.1, U5.1 (C1+)
unnamed: C11.2, U5.3 (C1-)
unnamed: C12.1, U5.5 (C2-)
unnamed: C12.2, U5.4 (C2+)
unnamed: C13.2, U5.6 (VS-)
unnamed: D1.2 (A), R8.1
unnamed: D2.2 (A), D3.1 (K), J2.1
unnamed: D4.1 (K), J1.3, R11.1
unnamed: D4.2 (K), J1.1, R10.1
unnamed: D5.1 (K), J4.1, U5.14 (T1OUT)
unnamed: D6.1 (K), J4.2, U5.13 (R1IN)
unnamed: D7.1 (K), J5.1, R18.1
unnamed: D7.2 (K), J5.3, R17.1
unnamed: D11.1 (K), J6.6, R21.2
unnamed: D11.2 (K), J6.7, R22.2
unnamed: R2.1, U1.3 (Out2a)
unnamed: R3.1, U1.1 (Out1a)
unnamed: R6.2, U2.1
unnamed: R7.1, U2.6
unnamed: R12.2, U7.1
unnamed: R13.2, U6.1
unnamed: R14.2, U5.12 (R1OUT)
unnamed: R15.2, U5.11 (T1IN)
unnamed: R16.2, U8.1
unnamed: R19.1, U7.6
unnamed: R20.1, U6.6
unnamed: U4.7 (XTAL1/PB6), Y1.1
unnamed: U4.8 (XTAL2/PB7), Y1.3
R1: R12.1, U4.10 (PD6)
R1A: D10.1 (K), J6.4, R19.2
R2: R13.1, U4.11 (PD7)
R2A: D10.2 (K), J6.5, R20.2
R3: R16.1, U4.9 (PD5)
R3A: D8.1 (K), D8.2 (K), J6.1, U8.6
R4: R6.1, U4.2 (PD4)
R4A: R7.2, U1.7 (In1a)
R4B: U1.8 (In1b), U2.4
RESET: C1.2, J3.5, R1.2, U4.29 (~RESET/PC6)
S1: R18.2, U4.23 (PC0)
S2: R17.2, U4.24 (PC1)
S3: R3.2, U4.27 (PC4)
S4: R2.2, U4.28 (PC5)
S5: R10.2, U4.26 (PC3)
S6: R11.2, U4.25 (PC2)
SCK: J3.3, U4.17 (PB5)
Throttle: C3.2, D9.2 (K), J6.3, R9.2
V1: R9.1, U4.1 (PD3)

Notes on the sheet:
Microcontroller
GND
Voltage Sense
SCK
MOSI
PWM CV Output
Relay Outputs
Power Supply
ICSP
SPM Connector 11+21+comm
REV
MISO
Throttle
Switch Input
Remootio-3 Module
FWD
Battery
DCE
Home(NC)
TxD
Console Interface
Aux Input
PWR
AUX
Indicator
RxD

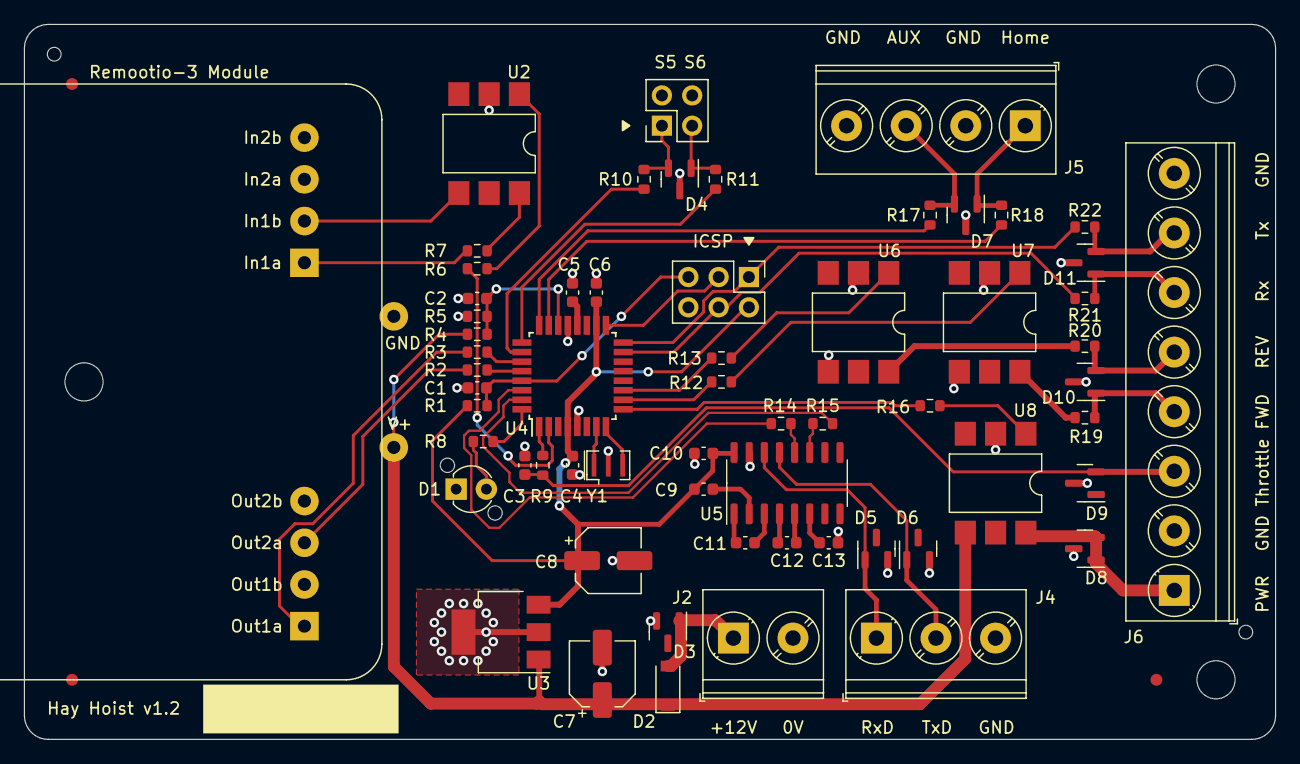
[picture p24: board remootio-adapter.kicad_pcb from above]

Board: 2 copper layers, 105.0 x 60.0 mm, 63 parts (0 on the bottom side), 58 nets.

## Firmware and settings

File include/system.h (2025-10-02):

// SPDX-License-Identifier: MIT

#ifndef SYSTEM_H
#define SYSTEM_H
#include <avr/io.h>

// Define missing IO regs - fixed in avr-libc 2.2
#ifndef PORTE
#define PORTE _SFR_IO8(0x0E)
#define UBRR1L  _SFR_MEM8(0xCC)
#define UCSR1A  _SFR_MEM8(0xC8)
#define UCSR1B  _SFR_MEM8(0xC9)
#define UCSR1C  _SFR_MEM8(0xCA)
#define UDR1    _SFR_MEM8(0xCE)
#endif // PORTE

// Default user settings
#define DEFAULT_P1	1250U	// 12.5s H -> P1
#define DEFAULT_P2	1500U	// 15s P1 -> P2
#define DEFAULT_F	30U	// 30 minutes, triggers P1->M_H
#define DEFAULT_NF	0U	// Feeds/week disabled
#define DEFAULT_MAN	400U	// 4s MAN adjustment
#define DEFAULT_H	4000U	// 40s Max return home time
#define DEFAULT_HR	250U	// 2.5s Home retry timeout
#define DEFAULT_S	60U	// 60 minutes safe time, triggers M_H
#define DEFAULT_PK	0U	// Default Console PIN

// Fixed voltage threshold
#define LOWVOLTS	0x4a	// ~11.8V

// Auto lowering voltage threshold
#define NIGHTVOLTS	0x53	// ~13.2V
#define OVRNONE		0x00	// No voltage override
#define OVRNIGHT	0x01	// Flag override of night volts
#define OVRLOW		0x02	// Flag override of low voltage

// Define I/O aliases, Refer: pcb/m328pb_portpins.pdf
#define S1	0		// PORTC.0
#define S2	1U		// PORTC.1
#define S6	2U		// PORTC.2
#define S5	3U		// PORTC.3
#define S3	4U		// PORTC.4
#define S4	5U		// PORTC.5
#define LED	2U		// PORTD.2
#define V1	3U		// PORTD.3
#define R4	4U		// PORTD.4
#define R3	5U		// PORTD.5
#define R1	6U		// PORTD.6
#define R2	7U		// PORTD.7
#define A1	3U		// PORTE.3:ADC7
#define IMASK	(_BV(S1)|_BV(S2)|_BV(S3)|_BV(S4)|_BV(S5)|_BV(S6))
#define OMASK	(_BV(LED)|_BV(V1)|_BV(R1)|_BV(R2)|_BV(R3)|_BV(R4))
#define SYSTICK	GPIOR0

// Non-volatile data addresses
#define NVM_BASE	0x3e0
#define NVM_P1		(NVM_BASE + 0)
#define NVM_P2		(NVM_BASE + 0x2)
#define NVM_MAN		(NVM_BASE + 0x4)
#define NVM_H		(NVM_BASE + 0x6)
#define NVM_F		(NVM_BASE + 0x8)
#define NVM_NF		(NVM_BASE + 0xa)
#define NVM_SPMOFT	(NVM_BASE + 0xc)
#define NVM_RSV0E	(NVM_BASE + 0xe)
#define NVM_SEEDOFT	(NVM_BASE + 0x10)
#define NVM_KEY		(NVM_BASE + 0x12)
#define NVM_KEYVAL	0x55aa
#define NVM_HR		(NVM_BASE + 0x14)
#define NVM_PK		(NVM_BASE + 0x16)
#define NVM_RSV18	(NVM_BASE + 0x18)
#define NVM_RSV1A	(NVM_BASE + 0x1a)
#define NVM_RSV1C	(NVM_BASE + 0x1c)
#define NVM_RSV1E	(NVM_BASE + 0x1e)

// Random seed area
#define SEEDOFT_LEN	NVM_BASE

// Timing estimator (for 7812.5 Hz / 78 timer)
#define ONEMINUTE	6000U

// One week of minutes
#define ONEWEEK		10080U

// Motor enable/disable delay time
#define MOTOR_DELAY	0x2710	// ~ 20ms
#define MOTOR_OFFTIME	0xc350	// ~ 0.1s
#define MOTOR_OFFCOUNT	2U

// Output function labels
#define FWD		R1
#define REV		R2
#define PWR		R3
#define ATP1		R4
#define THROTTLE	V1

// Input switch triggers (asserted after debouncing via read_input)
#define TRIGGER_HOME	_BV(S1)
#define TRIGGER_UP	_BV(S3)
#define TRIGGER_DOWN	_BV(S4)
#define TRIGMASK	(TRIGGER_HOME|TRIGGER_UP|TRIGGER_DOWN)

enum machine_state {
	state_stop,
	state_stop_h_p1,
	state_stop_p1_p2,
	state_at_h,
	state_at_p1,
	state_at_p2,
	state_move_h_p1,
	state_move_p1_p2,
	state_move_h,
	state_move_man,
	state_error,
};

// Note: counters p1 and p2 are preserved across move/stop transitions:
//       MOVE H-P1 <-> STOP H-P1
//       MOVE P1-P2 <-> STOP P1-P2
struct state_machine {
	uint8_t state;		// machine state
	uint8_t error;		// error flag
	uint8_t bstate;		// current accepted input state
	uint16_t p1;		// elapsed 0.01s moving h->p1
	uint16_t p1_timeout;	// target elapsed p1
	uint16_t p2;		// elapsed 0.01s moving p1->p2
	uint16_t p2_timeout;	// target elapsed p2
	uint16_t man_timeout;	// max manual adjust
	uint16_t h_timeout;	// maximum h movement
	uint16_t f_timeout;	// maximum minutes at p1
	uint16_t nf;		// number of feeds/day
	uint16_t nf_timeout;	// target minutes for h->p1
	uint16_t clock;		// 0.01s system clock
	uint16_t count;		// 0.01s state counter
	uint16_t mincount;	// 0.01s state counter for determining minutes
	uint16_t minutes;	// minute state counter
	uint16_t hr_timeout;	// home retry timeout
	uint16_t pk;		// serial console passkey
};

// global system variable
extern struct state_machine feed;

// global system version
extern uint16_t sw_version;

// Function prototypes
void write_word(uint16_t addr, uint16_t val);
uint16_t read_word(uint16_t addr);
uint8_t read_inputs(void);
void save_config(uint16_t addr, uint16_t val);
void system_init(void);

#endif // SYSTEM_H

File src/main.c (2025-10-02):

// SPDX-License-Identifier: MIT

/*
 * AVR m328p (Nano) Serial "PLC"
 */
#include <stdint.h>
#include <stdlib.h>
#include <avr/sleep.h>
#include <avr/wdt.h>
#include <util/delay_basic.h>
#include "system.h"
#include "console.h"

static void flag_error(void)
{
	feed.error = 1U;
}

static void clear_error(void)
{
	feed.error = 0;
}

static void read_voltage(void)
{
	if (ADCH < LOWVOLTS) {
		// Set Indicator
		PORTD |= _BV(LED);
	} else {
		// Clear Indicator
		PORTD &= (uint8_t) ~ _BV(LED);
	}
}

static uint8_t check_voltage(uint8_t override)
{
	uint8_t curvolts = ADCH;
	if (curvolts < LOWVOLTS) {
		return override & OVRLOW;
	} else {
		// allow any set override
		return (override || curvolts >= NIGHTVOLTS);
	}
}

static void motor_start(void)
{
	PORTD |= _BV(PWR);	// enable controller power
	_delay_loop_2(MOTOR_DELAY);	// pause for controller
	PORTD |= _BV(THROTTLE);	// raise throttle CV
}

static void motor_stop(void)
{
	PORTD &= (uint8_t) ~ _BV(THROTTLE);	// lower throttle CV
	_delay_loop_2(MOTOR_DELAY);	// pause to allow CV to settle
	PORTD &= (uint8_t) ~ (_BV(PWR) | _BV(FWD) | _BV(REV));	// disable
	// busy wait to allow motor roll down
	uint8_t count = 0;
	while (count < MOTOR_OFFCOUNT) {
		wdt_reset();
		_delay_loop_2(MOTOR_OFFTIME);
		++count;
	}
}

static void motor_reverse(void)
{
	PORTD |= _BV(REV);
}

static void motor_forward(void)
{
	PORTD |= _BV(FWD);
}

static void set_state(uint8_t newstate)
{
	feed.state = newstate;
	feed.count = 0;
	feed.mincount = 0;
	feed.minutes = 0;
	console_showstate(feed.state, feed.error, ADCH);
}

static void stop_at(uint8_t newstate)
{
	set_state(newstate);
	motor_stop();
}

static void set_randfeed(void)
{
	if (feed.nf) {
		uint16_t period = ONEWEEK / feed.nf;
		if (period) {
			uint16_t oft = period >> 1;
			// randval has range 0 to 0x7fffffff inclusive
			uint32_t randval = (uint32_t) random();
			uint32_t tmp =
			    ((uint32_t) (period) * (randval >> 13) +
			     (1UL << 17)) >> 18;
			feed.nf_timeout = oft + (uint16_t) (tmp);
		} else {
			feed.nf_timeout = 0;
		}
	} else {
		feed.nf_timeout = 0;
	}
	if (feed.nf_timeout) {
		console_showval("Feed in (min): ", feed.nf_timeout);
	}
}

static void stop_at_home(void)
{
	stop_at(state_at_h);
	clear_error();
	// Signal AT H state to Remootio
	PORTD &= (uint8_t) ~ _BV(ATP1);
	set_randfeed();
}

static void move_up(uint8_t newstate)
{
	if ((feed.bstate & TRIGGER_HOME) == 0) {
		set_state(newstate);
		motor_reverse();
		motor_start();
	} else {
		console_write("Sensor error\r\n");
		flag_error();
		stop_at(state_stop);
	}
}

static void move_down(uint8_t newstate)
{
	set_state(newstate);
	motor_forward();
	motor_start();
}

static void trigger_p1(void)
{
	if (feed.state == state_move_h_p1) {
		console_write("Trigger: p1\r\n");
		stop_at(state_at_p1);
		// Signal AT P1 state to Remootio
		PORTD |= _BV(ATP1);
	} else {
		console_write("Spurious P1 trigger\r\n");
	}
}

static void trigger_reset(void)
{
	console_write("Trigger: reset\r\n");
	stop_at(state_stop);
}

static void trigger_p2(void)
{
	if (feed.state == state_move_p1_p2) {
		console_write("Trigger: p2\r\n");
		stop_at(state_at_p2);
	} else {
		console_write("Spurious P2 trigger\r\n");
	}
}

static void trigger_man(void)
{
	if (feed.state == state_move_man) {
		console_write("Trigger: man\r\n");
		stop_at(state_stop);
	} else {
		console_write("Spurious Man trigger\r\n");
	}
}

static void trigger_max(void)
{
	if (feed.state == state_move_h) {
		console_write("Trigger: max\r\n");
		flag_error();	// failed to reach home
		stop_at(state_stop);
	} else {
		console_write("Spurious Max trigger\r\n");
	}
}

static void trigger_up(void)
{
	console_write("Trigger: up\r\n");
	switch (feed.state) {
	case state_stop:
	case state_stop_h_p1:
	case state_stop_p1_p2:
	case state_at_p1:
	case state_at_p2:
		move_up(state_move_h);
		break;
	case state_move_h_p1:
		stop_at(state_stop_h_p1);
		break;
	case state_move_p1_p2:
		stop_at(state_stop_p1_p2);
		break;
	case state_move_h:
	case state_move_man:
		stop_at(state_stop);
		break;
	case state_at_h:
	default:
		console_write("Spurious UP trigger\r\n");
		break;
	}
}

static void trigger_down(uint8_t override)
{
	console_write("Trigger: down\r\n");
	switch (feed.state) {
	case state_stop:
		move_down(state_move_man);
		break;
	case state_stop_h_p1:
		move_down(state_move_h_p1);
		break;
	case state_stop_p1_p2:
		move_down(state_move_p1_p2);
		break;
	case state_at_h:
		if (check_voltage(override)) {
			move_down(state_move_h_p1);
			feed.p1 = 0;
		} else {
			console_write("Trigger low voltage\r\n");
			stop_at_home();
		}
		break;
	case state_at_p1:
		move_down(state_move_p1_p2);
		feed.p2 = 0;
		break;
	case state_at_p2:
		move_down(state_move_man);
		break;
	case state_move_h_p1:
		stop_at(state_stop_h_p1);
		break;
	case state_move_p1_p2:
		stop_at(state_stop_p1_p2);
		break;
	case state_move_h:
	case state_move_man:
		stop_at(state_stop);
		break;
	default:
		console_write("Spurious DOWN trigger\r\n");
		break;
	}
}

static void trigger_home(void)
{
	console_write("Trigger: home\r\n");
	switch (feed.state) {
	case state_stop:
	case state_move_h:
		stop_at_home();
		break;
	case state_at_h:
		// reset state counter for home-retry timeout
		feed.count = 0;
		break;
	case state_at_p1:
		// do nothing
		console_write("Ignore home trigger\r\n");
		break;
	case state_move_h_p1:
		// after 0.5s, might be tangled cord - flag error and stop
		if (feed.count > 50) {
			console_write("Home trigger/tangle\r\n");
			flag_error();
			stop_at(state_stop);
		}
		break;
	default:
		// spurious home sense - flag error and stop
		console_write("Spurious Home trigger\r\n");
		flag_error();
		stop_at(state_stop);
		break;
	}
}

static void read_triggers(void)
{
	uint8_t triggers = read_inputs();
	if (triggers & TRIGMASK) {
		if (triggers & TRIGGER_HOME) {
			// Transition to home will mask concurrent trigs
			trigger_home();
		} else {
			if (triggers & TRIGGER_DOWN) {
				// remootio may override night voltage
				trigger_down(OVRNIGHT);
			}
			if (triggers & TRIGGER_UP) {
				// up cancels a concurrent down
				trigger_up();
			}
		}
	}
}

static void read_timers(void)
{
	uint16_t thresh;
	feed.count++;
	feed.mincount++;
	switch (feed.state) {
	case state_move_h_p1:
		feed.p1++;
		if (feed.p1 > feed.p1_timeout) {
			trigger_p1();
		}
		break;
	case state_move_p1_p2:
		feed.p2++;
		if (feed.p2 > feed.p2_timeout) {
			trigger_p2();
		}
		break;
	case state_move_man:
		if (feed.count > feed.man_timeout) {
			trigger_man();
		}
		break;
	case state_move_h:
		if (feed.error) {
			thresh = feed.man_timeout;
		} else {
			thresh = feed.h_timeout;
		}
		if (feed.count > thresh) {
			trigger_max();
		}
		break;
	case state_at_p1:
		if (feed.f_timeout) {
			if (feed.minutes >= feed.f_timeout) {
				trigger_up();
			}
		}
		break;
	case state_at_h:
		if (feed.nf_timeout > 0 && feed.minutes >= feed.nf_timeout) {
			trigger_down(OVRNONE);
		} else if (feed.hr_timeout > 0 && feed.count > feed.hr_timeout) {
			if ((feed.bstate & TRIGGER_HOME) == 0) {
				console_write("Trigger: notathome\r\n");
				move_up(state_move_h);
			} else {
				feed.count = 0;
			}
		}
		break;
	case state_stop:
	case state_stop_p1_p2:
	case state_at_p2:
		if (feed.minutes >= DEFAULT_S) {
			console_write("Safe time reached\r\n");
			trigger_up();
		}
		break;
	default:
		break;
	}
	if (feed.mincount >= ONEMINUTE) {
		feed.minutes++;
		feed.mincount = 0;
	}
}

static void update_state(uint8_t clock)
{
	feed.clock++;
	read_triggers();
	read_timers();
	if (clock == 0) {
		read_voltage();
	}
}

static void show_value(struct console_event *event)
{
	switch (event->key) {
	case 0x10:
		// double auth
		console_write("OK\r\n");
		break;
	case 0x31:
		console_showval("H-P1 = ", feed.p1_timeout);
		break;
	case 0x32:
		console_showval("P1-P2 = ", feed.p2_timeout);
		break;
	case 0x66:
		console_showval("Feed = ", feed.f_timeout);
		break;
	case 0x68:
		console_showval("H = ", feed.h_timeout);
		break;
	case 0x6e:
		console_showval("Feeds/week = ", feed.nf);
		break;
	case 0x6d:
		console_showval("Man = ", feed.man_timeout);
		break;
	case 0x70:
		console_showval("PIN = ", feed.pk);
		break;
	case 0x72:
		console_showval("H-Retry = ", feed.hr_timeout);
		break;
	default:
		console_write("Unknown value\r\n");
		break;
	}
}

static void update_value(struct console_event *event)
{
	switch (event->key) {
	case 0x10:
		// double auth
		console_write("OK\r\n");
		break;
	case 0x31:
		if (event->value) {
			feed.p1_timeout = event->value;
		}
		console_showval("H-P1 = ", feed.p1_timeout);
		save_config(NVM_P1, feed.p1_timeout);
		break;
	case 0x32:
		if (event->value) {
			feed.p2_timeout = event->value;
		}
		console_showval("P1-P2 = ", feed.p2_timeout);
		save_config(NVM_P2, feed.p2_timeout);
		break;
	case 0x66:
		feed.f_timeout = event->value;
		console_showval("Feed = ", feed.f_timeout);
		save_config(NVM_F, feed.f_timeout);
		break;
	case 0x6e:
		feed.nf = event->value;
		console_showval("Feeds/week = ", feed.nf);
		save_config(NVM_NF, feed.nf);
		if (feed.state == state_at_h) {
			set_randfeed();
		}
		break;
	case 0x6d:
		if (event->value) {
			feed.man_timeout = event->value;
		}
		console_showval("Man = ", feed.man_timeout);
		save_config(NVM_MAN, feed.man_timeout);
		break;
	case 0x68:
		if (event->value) {
			feed.h_timeout = event->value;
		}
		console_showval("H = ", feed.h_timeout);
		save_config(NVM_H, feed.h_timeout);
		break;
	case 0x70:
		feed.pk = event->value;
		console_showval("PIN = ", feed.pk);
		save_config(NVM_PK, feed.pk);
		break;
	case 0x72:
		feed.hr_timeout = event->value;
		console_showval("H-Retry = ", feed.hr_timeout);
		save_config(NVM_HR, feed.hr_timeout);
		break;
	default:
		console_write("Unknown value\r\n");
		break;
	}
}

static void show_values(void)
{
	console_write("Values:\r\n");
	console_showval("\tFirmware = v", sw_version);
	console_showval("\tH-P1 = ", feed.p1_timeout);
	console_showval("\tP1-P2 = ", feed.p2_timeout);
	console_showval("\tMan = ", feed.man_timeout);
	console_showval("\tH = ", feed.h_timeout);
	console_showval("\tH-Retry = ", feed.hr_timeout);
	console_showval("\tFeed = ", feed.f_timeout);
	console_showval("\tFeeds/week = ", feed.nf);
	console_showval("\tMin = ", feed.minutes);
	console_write("\r\n");
}

static void show_status(void)
{
	console_showstate(feed.state, feed.error, ADCH);
}

static void handle_event(struct console_event *event)
{
	switch (event->type) {
	case event_getvalue:
		show_value(event);
		break;
	case event_setvalue:
		update_value(event);
		break;
	case event_status:
		show_status();
		break;
	case event_values:
		show_values();
		break;
	case event_down:
                // console trigger may override low voltage
		trigger_down(OVRLOW);
		break;
	case event_up:
		trigger_up();
		break;
	default:
		break;
	}
}

void main(void)
{
	uint8_t lt = 0;
	uint8_t nt;
	struct console_event event;
	system_init();
	trigger_reset();
	console_flush();
	do {
		sleep_mode();
		nt = SYSTICK;
		if (nt != lt) {
			update_state(nt);
			lt = nt;
		}
		console_read(&event);
		if (event.type != event_none) {
			handle_event(&event);
		}
		wdt_reset();
	} while (1);
}

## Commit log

2024-06-13 Ignore datasheets and prototype layout
2024-06-13 Functional prototype upgrade
2024-07-22 Add v1.0/m328pb PCB
    [m328pb_portpins.ods, remootio-adapter.kicad_pcb, remootio-adapter.kicad_sch]
2024-07-22 Add watchdog timer to main loop
2024-07-22 Remove brake cv and update low voltage logic
2024-07-22 Update prototype docs to match final version
2024-07-25 Document special case logic and remove duplicate motor delay
2024-07-28 Add spmtool config file and update readme
    [spm_config.txt]
2024-07-30 Update for m328pb and final PCB layout
2024-07-30 Revise PCB layout for production board v1.1
    [remootio-adapter.kicad_pcb, remootio-adapter.kicad_sch]
2024-07-30 Update schematic and preview for board v1.1
2024-07-31 Add mounting hole diagram
    [remootio-adapter.kicad_pcb]
2024-08-06 Minor cosmetic footprint adjustment
    [remootio-adapter.kicad_pcb, remootio-adapter.kicad_sch]
2024-08-06 Jostle footprints onto 0.5mm grid and change terminals to 5mm pitch
    [remootio-adapter.kicad_pcb, remootio-adapter.kicad_sch]
2024-08-06 Adjust motor controller settings at boot if required
2024-08-07 Replace C7 and C8 with EEEFN1V220R
    [remootio-adapter.kicad_pcb, remootio-adapter.kicad_sch]
2024-08-13 Avoid reboot loop on failed spm setting
    [spmcheck.c, system.c, system.h]
2024-08-13 Update readme with connector info
2024-08-13 Add part nos for screw terminals
    [remootio-adapter.kicad_sch]
2024-08-14 Add delay after motor off and reduce max battery current to 85%
    [spm_config.txt]
2024-08-16 Alter remootio power pads and add fiducials
    [remootio-adapter.kicad_pcb]
2024-08-16 Add basic mech hole footprint
2024-08-27 Begin assembly instruction
2024-08-27 Add missing connector images
2024-08-28 Add motor controller preparation
2024-09-28 Update assembly instruction
2024-12-08 Fix config key filter mismatch
2025-04-11 v25001 home retry and console PIN
2025-06-27 Use spinbox for position timers
